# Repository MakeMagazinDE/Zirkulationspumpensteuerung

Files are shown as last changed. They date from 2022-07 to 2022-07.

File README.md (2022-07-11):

GitHub Logo

Maker Media GmbH

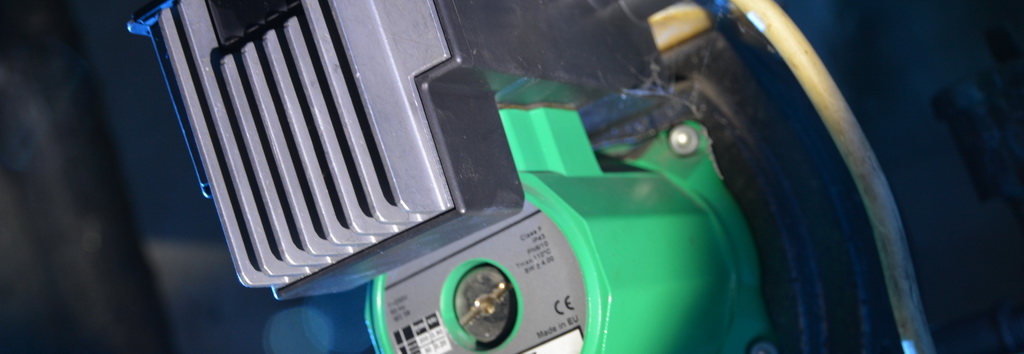
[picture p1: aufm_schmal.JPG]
Aufmacher


# Warmwasser-Sparpumpe

## für Heizkessel mit Zirkulationskreislauf

Heizkessel mit Brauchwasser-Erwärmung sind in der Regel mit einer Pumpe für den Warmwasser-Zirkulationskreislauf ausgerüstet, die regelmäßig anspringt, damit auch an entfernten Zapfstellen stets heißes Wasser entnommen werden kann. Diese Komfort-Funktion spart zwar Wasser, verbraucht aber unnötig Energie. Unsere Spar-Schaltung reduziert die Verschwendung auf ein Minimum.

## Stückliste

* C1:                  100uF/10V                                                    
* ESP-12E/F:           ESP8266-Board oder Wemos D1 Mini                                               
* F1:                  Sicherung 1,5A                                               
* JP1:                 3-Pin-Header RM 2.54mm für Temp.Sensor Dallas DS18B20        
* JP2:                 10-Pin-Header RM 2.54mm für Prog-Schnittstelle               
* PRINTTRAFO3.3V, 3W:  AC/DC-Wandler Meanwell IRM-01-3.3 oder ähnlich, 3,3V/1A      
* R1:                  1,5K                                                         
* R2:                  2,2K                                                         
* R3, R4:              10K                                                                                                               
* SSR__OMRONG3MB-202P: S102S02 SSR Solid State Relay                                
* VAR1:                VARISTOR 250V AC (optional)                                                 
* X1:                  Steckverbinder Phoenix MKDSN1,5/3-5,08   
* Schalterdose Feuchtraum
* Ggf. Schukostecker/Kupplung

Die Schaltung kann problemlos auf einer Lochraster-Platine aufgebaute werden, wenn netzspannungsführende Leitungen min. 5mm Abstand untereinander und 10mm Abstand zur Niederspannungsseite aufweisen. Beachten Sie die einschlägigen VDE-Vorschriften. Bei der Verwendung eines "nackten" ESP8266-Moduls anstelle des mit Stiftleisten ausgestatteten Wemos-Moduls ist einer (ggf. selbstgefertigte) Platine nötig. Das Layout für den Editor EAGLE finden Sie im entsprechenden Unterordner.

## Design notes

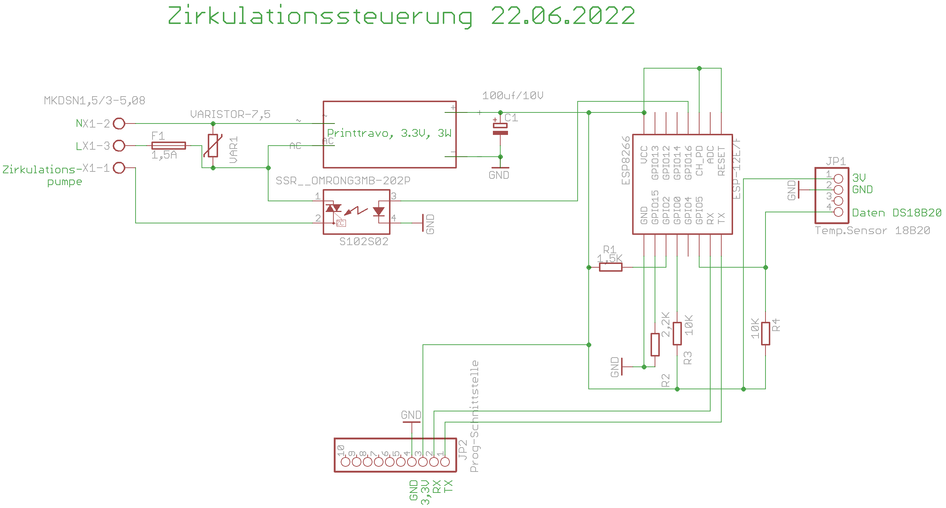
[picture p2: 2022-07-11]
schaltung.png

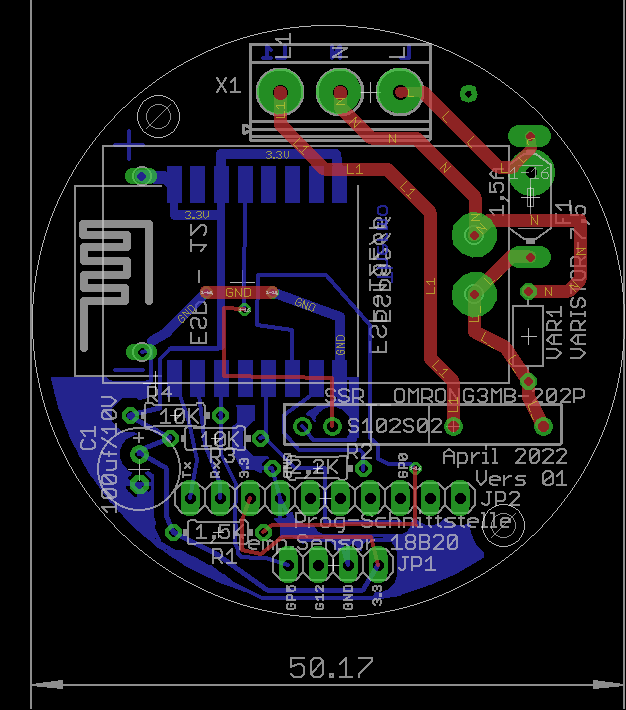
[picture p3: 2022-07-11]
layout_pic.png

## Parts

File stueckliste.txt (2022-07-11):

Partlist

Exported from MQTT-Zirkulation.sch at 22.06.2022 13:15

EAGLE Version 9.6.2 Copyright (c) 1988-2020 Autodesk, Inc.

Assembly variant: 

Part                Value              Device          Package         Library         Sheet

C1                  100uf/10V          CPOL-EUE2.5-7   E2,5-7          rcl             1
ESP-12E/F           ESP8266            ESP12SMD        ESP12-SMD       esp8266modules  1
F1                  1,5A               LITTLEFUSE      LITTLEFUSE      fuse            1
JP1                 Temp.Sensor 18B20  PINHD-1X4       1X04            pinhead         1
JP2                 Prog-Schnittstelle PINHD-1X10      1X10            pinhead         1
PRINTTRAFO3.3V,_3W  PRINTTRAFO         PRINTTRAFO      PRINTTRAFO      Uwes_lib        1
R1                  1,5K               R-EU_0204/7     0204/7          rcl             1
R2                  2,2K               R-EU_0204/7     0204/7          rcl             1
R3                  10K                R-EU_0204/7     0204/7          rcl             1
R4                  10K                R-EU_0204/7     0204/7          rcl             1
SSR__OMRONG3MB-202P S102S02            S102S02         S202S02         relay           1
VAR1                VARISTOR-7,5       VARISTOR-7,5    R-7,5           varistor        1
X1                  MKDSN1,5/3-5,08    MKDSN1,5/3-5,08 MKDSN1,5/3-5,08 con-phoenix-508 1

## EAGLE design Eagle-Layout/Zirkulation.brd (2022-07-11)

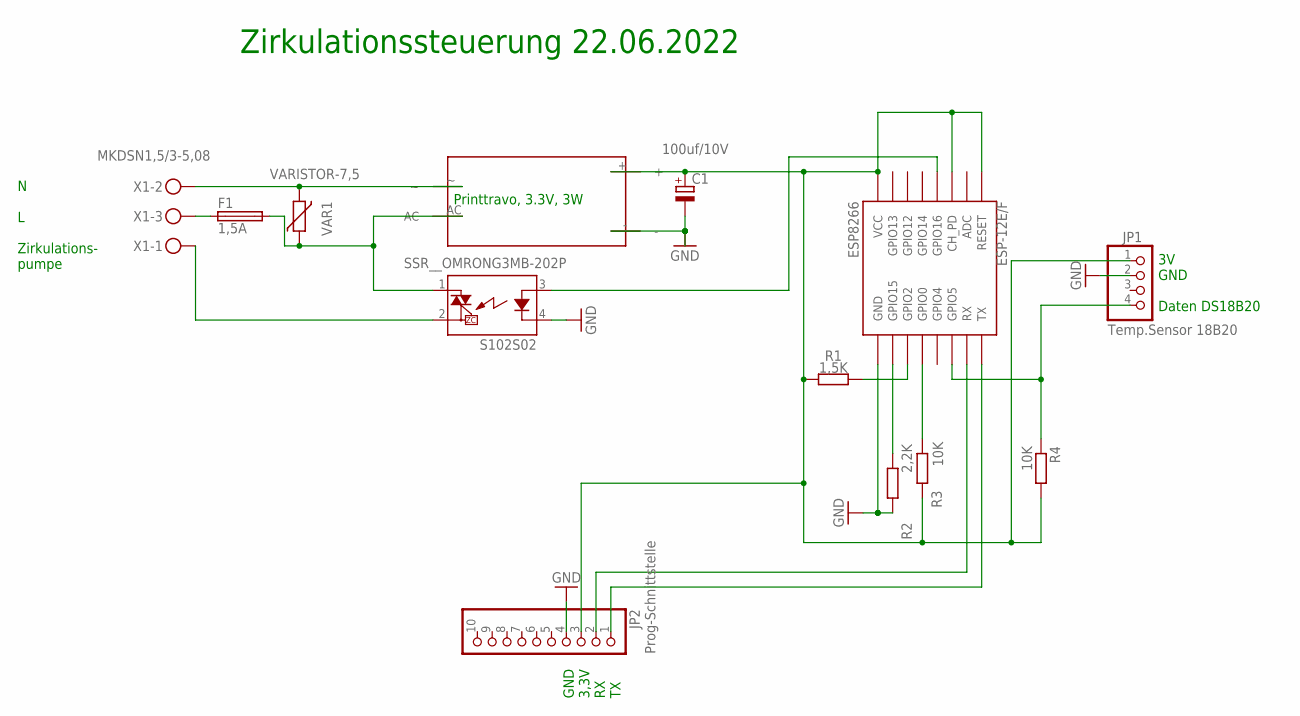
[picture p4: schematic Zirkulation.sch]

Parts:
C1: 100uf/10V; E2,5-7
ESP-12E/F: ESP8266; ESP12-SMD
F1: 1,5A; LITTLEFUSE
JP1: Temp.Sensor 18B20; 1X04
JP2: Prog-Schnittstelle; 1X10
PRINTTRAFO3.3V,_3W: PRINTTRAFO
R1: 1,5K; 0204/7
R2: 2,2K; 0204/7
R3, R4: 10K; 0204/7
SSR__OMRONG3MB-202P: S102S02; S202S02
VAR1: VARISTOR-7,5; R-7,5
X1: MKDSN1,5/3-5,08

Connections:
3.3V: C1.+, ESP-12E/F.CH_PD, ESP-12E/F.RESET, ESP-12E/F.VCC, JP1.1, JP2.3, PRINTTRAFO3.3V,_3W.+, R1.2, R3.2, R4.2
GND: C1.-, ESP-12E/F.GND, JP1.2, JP2.4, PRINTTRAFO3.3V,_3W.-, R2.1, SSR__OMRONG3MB-202P.4 (K)
GPIO0: ESP-12E/F.GPIO0, R3.1
GPIO2: ESP-12E/F.GPIO2, R1.1
GPIO5: ESP-12E/F.GPIO4 (GPIO5), JP1.4, R4.1
GPIO15: ESP-12E/F.GPIO15, R2.2
GPIO16: ESP-12E/F.GPIO16, SSR__OMRONG3MB-202P.3 (A)
L: F1.1, X1.3
L1: SSR__OMRONG3MB-202P.2 (DS2), X1.1
L_: F1.2, PRINTTRAFO3.3V,_3W.AC, SSR__OMRONG3MB-202P.1 (DS1), VAR1.1
N: PRINTTRAFO3.3V,_3W.~, VAR1.2, X1.2
RX: ESP-12E/F.RXD0 (RX), JP2.2
TX: ESP-12E/F.TXD0 (TX), JP2.1

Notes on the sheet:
Printtravo, 3.3V, 3W
N L Zirkulations- pumpe
Zirkulationssteuerung 22.06.2022
3V GND Daten DS18B20
GND 3,3V RX TX

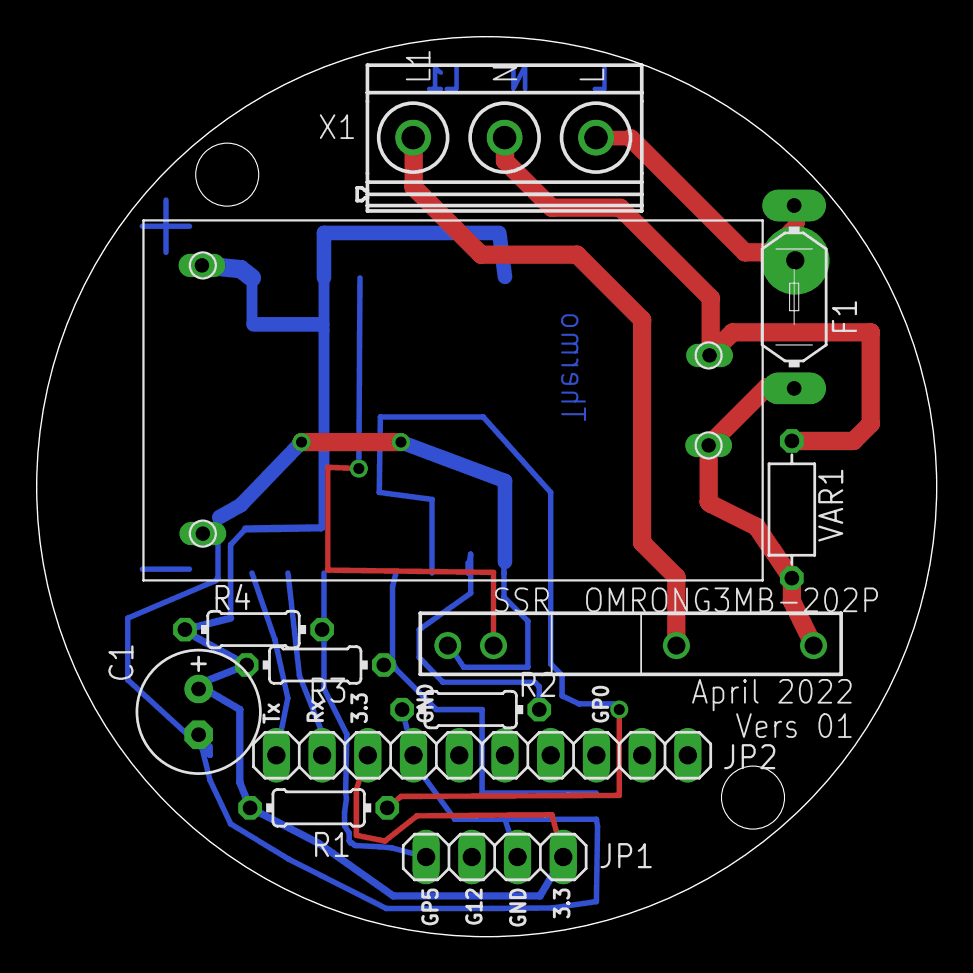
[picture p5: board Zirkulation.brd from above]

Board: 2 copper layers, 50.0 x 50.0 mm, 13 parts (1 on the bottom side), 13 nets.

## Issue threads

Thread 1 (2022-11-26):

Bitte Teileliste prüfen Relais ist EOL

mathdo, 2022-11-26:
Wäre schön, wenn Ihr die Teileliste überarbeiten und erweitern könntet.

- Ein oder zwei Alternativen für das Relais, da ich dieses SSR nicht mehr bei gängigen Händlern finden konnte (EOL). Auch wäre ein Hinweis zu einem geeigneten Varistor-Typ hilfreich.
- Hilfreich wären natürlich Teilelisten für gängige Elektronikhändler (Reichelt, Conrad, Pollin, ELV) bei dem alle Teile zu bekommen sind, sodass man die Bestellung nicht aufteilen muss ;-)
- Der vollständigkeithalber: Wieviel Verlustleistung müssen die Widerstände ab können?

Ein paar Hinweise bzw. ein Beispiel zum Layout auf Lochrasterplatine wäre natürlich auch schön (speziell wegen der im HEft erwähnten Isolationsabstände). Vielleicht dann auch keine runde Platine (vermutlich war die Idee diese in eine UP-Dose zu packen?).

Danke!

Noschvie, 2024-08-16:
@StefanBruens hast du diesen Algorithmus unter Tasmota zum Laufen gebracht? Danke!

StefanBruens, 2024-08-16:
@Noschvie - Ich hab das ganze mit einem ESP32(-C3) aufgebaut, und dann mittels Berry-Script implementiert. Macht das ganze wesentlich flexibler ...

Einen weiteren Unterschied gibt es bei mir noch, ich messe sowohl auf der Warmwasserleitung (um da Einschalten zu triggern, wie hier vorgeschlagen), als auch auf der Zirkulations-Rückleitung. Wenn letztere weniger als 10K Temperaturdifferenz zur WW-Leitung hat, wird abgeschaltet, das begrenzt die Laufzeiten der Pumpe sehr effektiv (morgens, bei der 1. Entnahme, Leitungen kalt, läuft die Pumpe dann ca. 5 Minuten, im Laufe des Tages bei "lauwarmen" Leitungen 2-3 Minuten). Das verringert sowohl die Stromkosten, als auch den Energieverlust auf der Rückleitung.

Noschvie, 2024-08-16:
Ist deine Lösung irgendwo im Web zugänglich?
Habe ebenso einen ESP32 mit zwei DS18B20 am WW Vor- und Rücklauf und möchten damit die Pumpe steuern...

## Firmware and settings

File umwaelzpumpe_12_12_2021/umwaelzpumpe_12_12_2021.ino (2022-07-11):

/*
 * Softwarestand 12.12.2021
 * Steuerung Umwaelzpumpe der Warmwasserheizung, 
 * wenn ca. 50-100ml heißes Wasser laeuft, ergibt es eine kleine Temperaturaenderung direkt am Anschlussrohr des
 * Heisswasserkessels. Die Umwaelzpumpe wird darauf hin eingeschaltet. Zwischen den Einschaltvorgängen 
 * der Pumpe muss eine Pause von mindestens 36 Minuten liegen. Wird über 24 h keine Anforderung registriert, 
 * wird wegen der thermischen Desinfektion ein Pumpenlauf gestartet.
*/
#include <OneWire.h>
#include <DallasTemperature.h>
#define ONE_WIRE_BUS 5 //D3: Dallas Tempsensor 18B20
#define pumpenpin 16 // SSR Anschluss um Pumpe zu steuern
#define TEMPERATURE_PRECISION 12   
OneWire oneWire(ONE_WIRE_BUS);
DallasTemperature sensors(&oneWire);
DeviceAddress Thermometer;
//************************************************************************************************************
void setup() {
  Serial.begin(115200);
  pinMode(pumpenpin, OUTPUT);
  pinMode(LED_BUILTIN, OUTPUT);
  sensors.begin();
  Serial.print("\nVersion vom 12.12.2021, \n\nLocating devices..."); Serial.print("Found "); 
  Serial.print(sensors.getDeviceCount(), DEC); Serial.println(" devices.");
  if (!sensors.getAddress(Thermometer, 0)) Serial.println("Unable to find address for Device 0"); 
  Serial.print("Device 0 Address: "); 
  for (uint8_t i = 0; i < 8; i++) {
    if (Thermometer[i] < 16) Serial.print("0"); Serial.print(Thermometer[i], HEX);//zero pad the address if necessary
  }
  Serial.println("");
  sensors.setResolution(Thermometer, TEMPERATURE_PRECISION); //hohe Genauigkeit
}
//************************************************************************************************************
void loop() {
  static float t[] = {0.0,  0.0,  0.0,  0.0,  0.0}; //letzten 5 Temepraturwerte speichern
  float temperatur_delta = 0.0;
  static unsigned long timer_24h = 0,timer_1Sekunde = 0, ausgabecnt = 0; //ausgabecount muss bis 86400 gehen, soviel Sekunden hat ein Tag
  static int cnt = 0;
  sensors.requestTemperatures(); // Send the command to get temperatures
  float temperatur = sensors.getTempCByIndex(0);
  Serial.print(++ausgabecnt); 
  Serial.print(" Counter, Software vom 09.11.2021, Temperatur betraegt: "); Serial.println(temperatur); 
  if(++cnt >= 5) cnt = 0;
  t[cnt] = temperatur;
  int cnt_alt = (cnt + 6) % 5;            // Es wird der Wert von vor 5 Messungen aus dem Ringpuffer ermittelt
  temperatur_delta = t[cnt]-t[cnt_alt]; // Temperaturdifferenz der letzten 5 Messzyklen bzw. Sekunden
  if(temperatur_delta >= 0.12) {        // kleinste Temeraturaenderung ist 0,06°C, 
    if(pumpe(true) == true) {           // wenn binnen 5 Sekunden > = 0.12°C gestiegen ist, Pumpe an! 
      ausgabecnt = 0;
      timer_24h = millis();             // 24h-Timer neu starten
    } 
  }
  else pumpe(false);
  if (millis() - timer_24h > 24*60*60*1000) { //1x am Tag soll Pumpe laufen wegen thermische Desinfektion (also vor allem im Urlaub)
    timer_24h = millis();
    if(pumpe(true) == true) ausgabecnt = 0;
  }     
  while((millis()) - timer_1Sekunde < 1000) yield();
  timer_1Sekunde = millis();
  digitalWrite(LED_BUILTIN, !digitalRead(LED_BUILTIN)); //eingebaute blaue LED blinkt im Sekundenrythmus, d.h. Programm laeuft
}
//*********************************************************************
boolean pumpe(boolean pumpe_soll_laufen) {
  static unsigned long timer_pumpenlaufzeit = 0, timer_pause = 0; //timer_pumpenlaufzeit: steuert Laufzeit der Pumpe, timer_pause steuert die Größe der Pause zwischen den Laufzeiten
  static boolean pumpe_laeuft = false;
  if(pumpe_soll_laufen == true && pumpe_laeuft == false && (millis() - timer_pause) > 36*60*1000) {        //Pumpe soll nur alle 30 Minuten 
    pumpe_laeuft = true;                                                                                   //laufen (36Min-6 Min Laufzeit = 30Min)
    digitalWrite(pumpenpin, HIGH);
    Serial.println("Pumpe ein");
    timer_pumpenlaufzeit = millis();
    timer_pause = millis();
    return(true);
  }
  if(pumpe_soll_laufen == false && pumpe_laeuft == true && (millis() - timer_pumpenlaufzeit) > 6*60*1000) { //Pumpe laeuft für 6 Minuten
    pumpe_laeuft = false;
    digitalWrite(pumpenpin, LOW);
    Serial.println("Pumpe aus");
  }
  return(false);
}
//*****************************************************************************************************
